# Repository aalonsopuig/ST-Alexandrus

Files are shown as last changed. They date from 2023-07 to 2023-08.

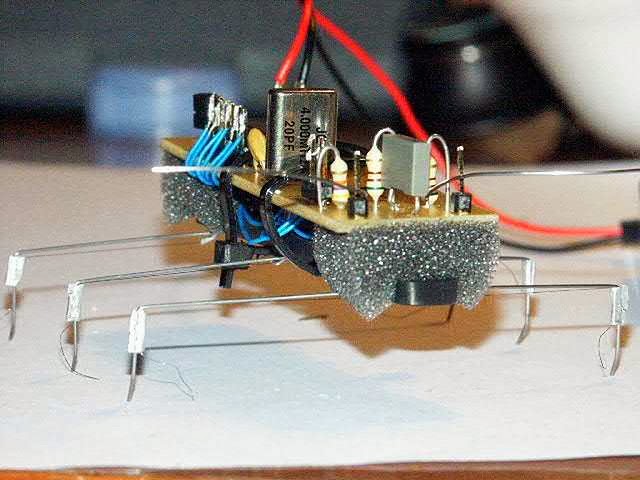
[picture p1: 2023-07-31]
st-alex.jpg

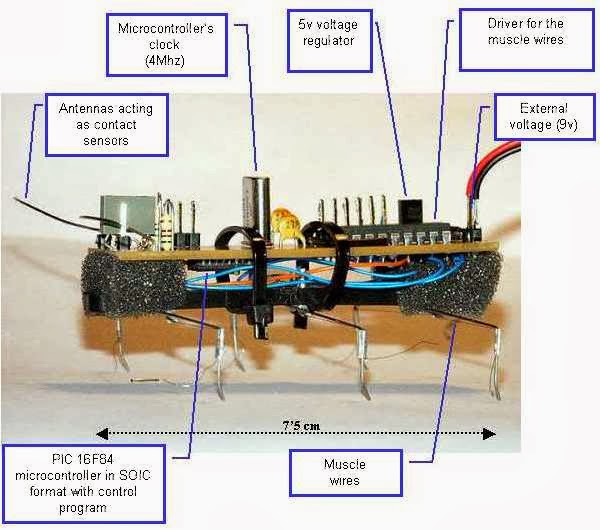
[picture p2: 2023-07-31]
enstparts.jpg

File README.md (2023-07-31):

ST-Alexandrus is an hexapod of one degrees of freedom by leg based on the structure of Stiquito (<a href="http://www.stiquito.com/">www.stiquito.com</a>). I made it on Dec. 2002<br />
<br />
The locomotion system is based on muscle wires of Nitinol.<br />
<br />
Its mission consists of moving as far as possible avoiding the obstacles that are in their way.<br />
<br />
<table align="center" cellpadding="0" cellspacing="0" class="tr-caption-container" style="margin-left: auto; margin-right: auto; text-align: center;"><tbody>
<tr><td style="text-align: center;"></td></tr>
<tr><td class="tr-caption" style="text-align: center;">ST-Alexandrus Robot</td></tr>
</tbody></table>
<br />
<b>Muscle Wires</b><br />
<br />
The muscle wire is an alloy (Nitinol) that belongs to the group of the so called materials with form memory. The wire is compressed between 3 and 5% of its length when warming up itself by the passage of an electrical current and return to its normal state when cooling off (annulling the passage of electrical current). The contraction is fast (0.5 sg), but the relaxation is slower as thicker is the muscle wire, varying between 0.7 sg for a wire of 37 micrometers and 14.5 sg for one of 375 micrometers.<br />
<br />
<div class="separator" style="clear: both; text-align: center;">
<object width="320" height="266" class="BLOGGER-youtube-video" classid="clsid:D27CDB6E-AE6D-11cf-96B8-444553540000" codebase="http://download.macromedia.com/pub/shockwave/cabs/flash/swflash.cab#version=6,0,40,0" data-thumbnail-src="https://ytimg.googleusercontent.com/vi/N188-MJZrzo/0.jpg"><param name="movie" value="https://youtube.googleapis.com/v/N188-MJZrzo&source=uds" /><param name="bgcolor" value="#FFFFFF" /><param name="allowFullScreen" value="true" /><embed width="320" height="266"  src="https://youtube.googleapis.com/v/N188-MJZrzo&source=uds" type="application/x-shockwave-flash" allowfullscreen="true"></embed></object></div>
<br />
These long times of relaxation and small ratios of compression will imply that the robot moves slowly, with very short and slowed down steps.<br />
<br />
<br />
<b>Legs structure</b><br />
<br />
The legs are made with steel wire and therefore they are relatively elastic.<br />
<br />
Each leg has an only muscle wire that moves backwards the leg when being compressed (applying electrical current).<br />
<br />
<div class="separator" style="clear: both; text-align: center;">
</div>
<br />
The meeting point between the leg and the ground is slightly inclined backwards to assure the adhesion to the ground in the backwards movements of the leg and to reduce this adhesion in the forwards movements of the leg, necessary to allow him to walk since when having an only degree of freedom, only could drag the legs over the ground.<br />
<br />
When we stop applying electrical current to the muscle wire it cools off and stretches to its rest position. Since the leg is of steel wire, its elasticity tends to move forwards the leg until its rest position.<br />
<br />
Due to this structure of legs the robot cannot walk backwards.<br />
<br />
<br />
<b>Electronic circuit</b><br />
<br />
Basically it is a control system by microcontroller PIC16F84 and a driver of 8 channels (open collector) of which will be used 6 to give to the muscle wires the current that need to be compressed.<br />
<br />
He has contact sensors (bumpers) in the frontal part (antennas) that allow to detect obstacles.<br />
<br />
Next is the electrical scheme:<br />
<br />
<div class="separator" style="clear: both; text-align: center;">
</div>
<br />
The circuit includes a diode to prevent errors with polarity when connecting the battery and a 5v regulator to be able to use external feeding to 9v.<br />
<br />
<div class="separator" style="clear: both; text-align: center;">
</div>
<br />
Terminals "PROG" allow ICSP programming (In Circuit Serial Programming) of the microcontroller already mounted in plate.<br />
<br />
Terminals "IZDA" (Left) and "DCHA" (Right) correspond to the connections to the muscle wires of the legs. All the muscle wires have on common end and the other connected to each one of these pins. The common end, that correspond with the union of the muscle wire with the leg of steel wire, will be connected to the positive of the battery, between the diode and the voltage regulator.<br />
<br />
<div class="separator" style="clear: both; text-align: center;">
</div>
<br />
&nbsp;<b>Software</b><br />
<br />
The programming has been made in C language, using the freeware cross compiler PICC Lite of HTSOFT<br />
<br />
The algorithm is simple. Simply it makes the robot move by moving the legs three by three so that they always form a support triangle. When one of the antennas detects an obstacle, the robot moves only the legs of a side one to one to force the turn since as it has been mentioned before, the robot cannot walk backwards.<br />
<br />
The code is suitably commented for its understanding.<br />
<br />
<br />

<br />

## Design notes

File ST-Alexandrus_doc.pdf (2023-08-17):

## ST-Alexandrus

ST-Alexandrus es un hexápodo de un grado de libertad por pata construido sobre la estructura de un Stiquito (www.stiquito.com).

El sistema de locomoción está basado en alambres musculares (muscle wires) de Nitinol. Las patas están formadas por alambres de acero.

Cada pata es controlada de forma independiente desde
una placa de control con microcontrolador PIC16F84.

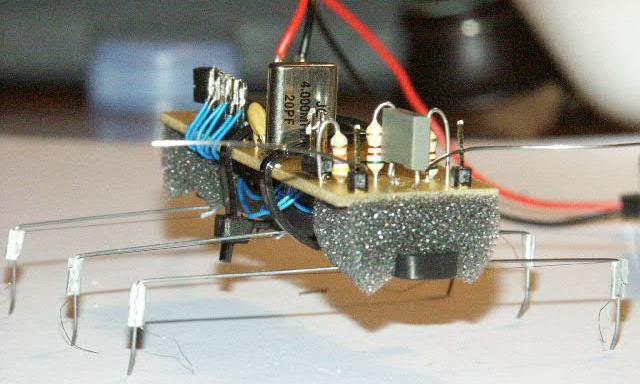
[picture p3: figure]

Posee sensores de contacto en la parte frontal que le permiten detectar obstáculos y aplicar algoritmos de giro.

### Construcción

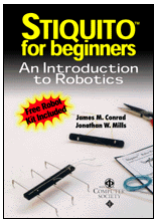
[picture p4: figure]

En primer lugar hay que montar la estructura de Stiquito. Dicha estructura se incluye como parte del libro “Stiquito for beginners” de James Conrad y Jonathan Mills.

Una vez montada la estructura se realiza el diseño de la electrónica. Básicamente se trata de un sistema de control por microcontrolador PIC16F84 y un driver de 8 canales para generar dar a los alambres musculares la corriente que necesitan para comprimirse.

A continuación se muestra es esquema eléctrico:

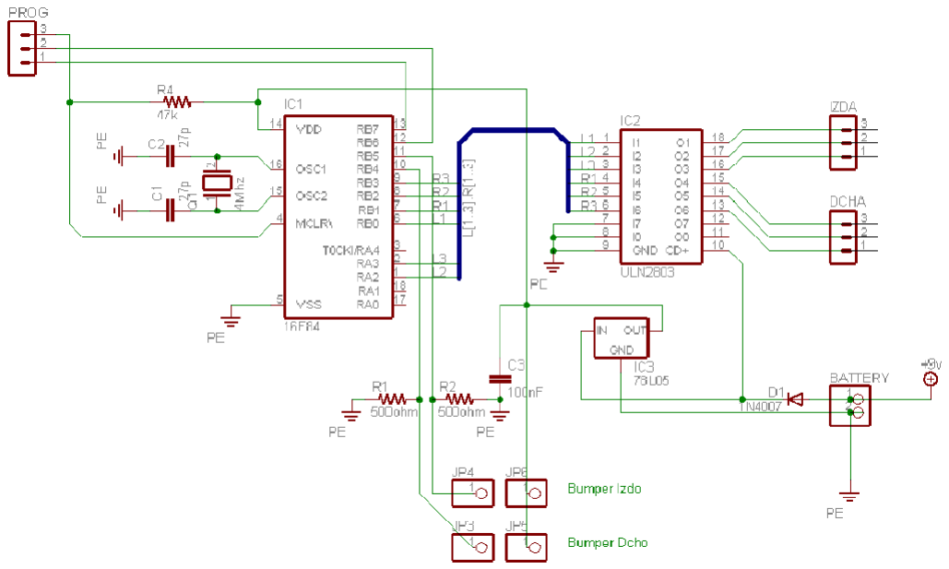
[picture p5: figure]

El circuito incluye un diodo para prevenir errores de polaridad al conectar la pila y un regulador a 5v para poder utilizar alimentación externa a 9v.

Los terminales “PROG” permiten la programación del microcontrolador desde una placa de grabación.

Los terminales “IZDA” y “DCHA” corresponden a las
conexiones a los alambres musculares de las patas. Todos
los alambres musculares tienen un extremo común y el otro conectado a cada una de estas patillas. El extremo común, que coincide con la unión con la pata de alambre de acero, quedará conectada al positivo de la batería, entre el diodo y el regulador de tensión.

Se montó el circuito en una protoboard y se programó el microcontrolador para comprobar el correcto resultado.

El diseño de la placa resultante es como sigue. En la
primera imagen se muestran las pistas y componentes. El
microcontrolador es el único componente que se situará en

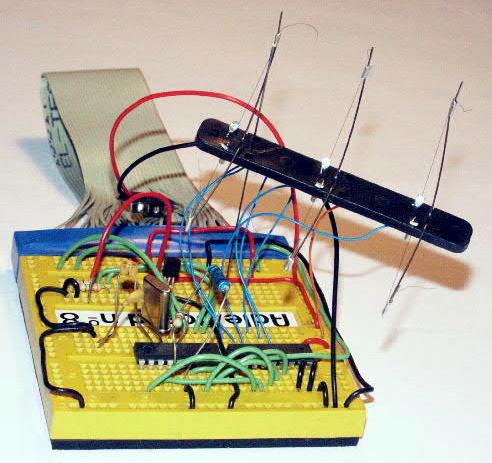
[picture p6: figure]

la parte inferior de la placa por ser de formato SOIC. Como se puede ver en la imagen hay un par de conexiones que deben hacerse mediante puentes.

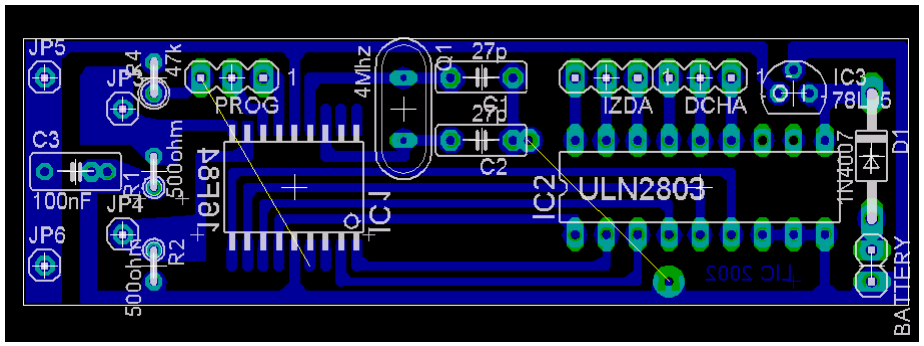
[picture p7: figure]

La segunda imagen corresponde a las pistas en inverso, tal como luego se imprimieron en transferible PNP.

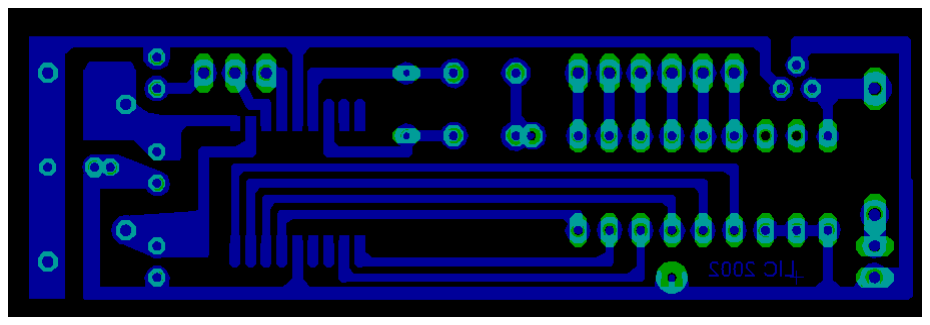
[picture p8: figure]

Una vez impreso en transferible PNP quedaría como se muestra a continuación:

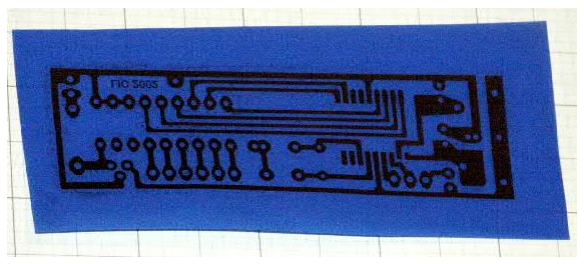
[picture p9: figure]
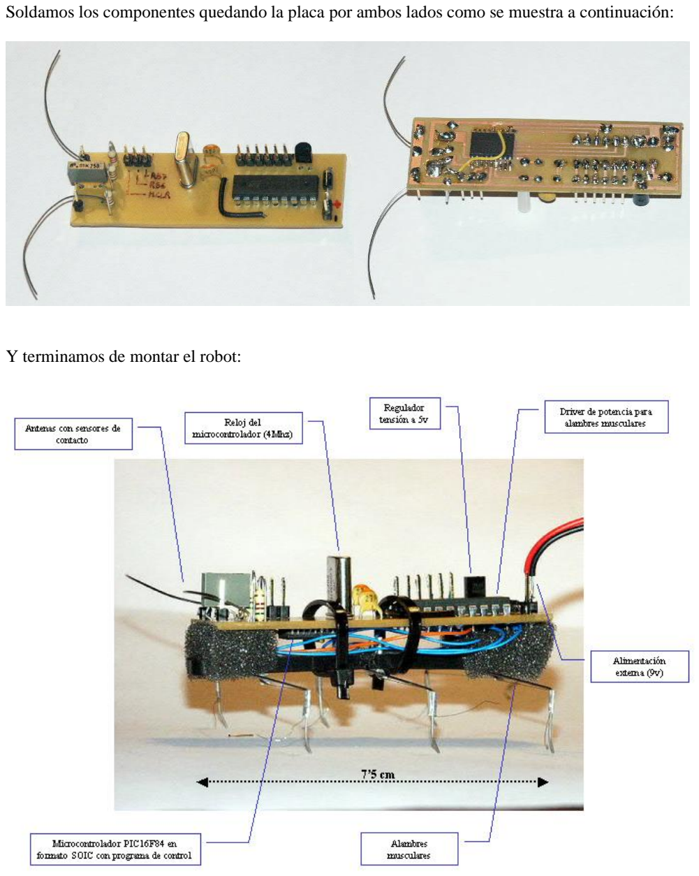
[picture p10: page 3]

Soldamos los componentes quedando la placa por ambos lados como se muestra a continuación:

Y terminamos de montar el robot:

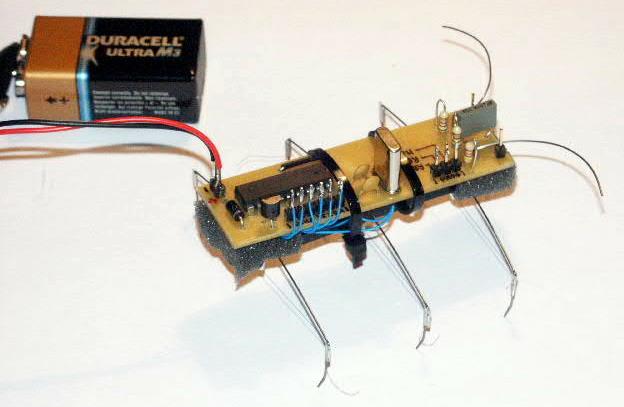
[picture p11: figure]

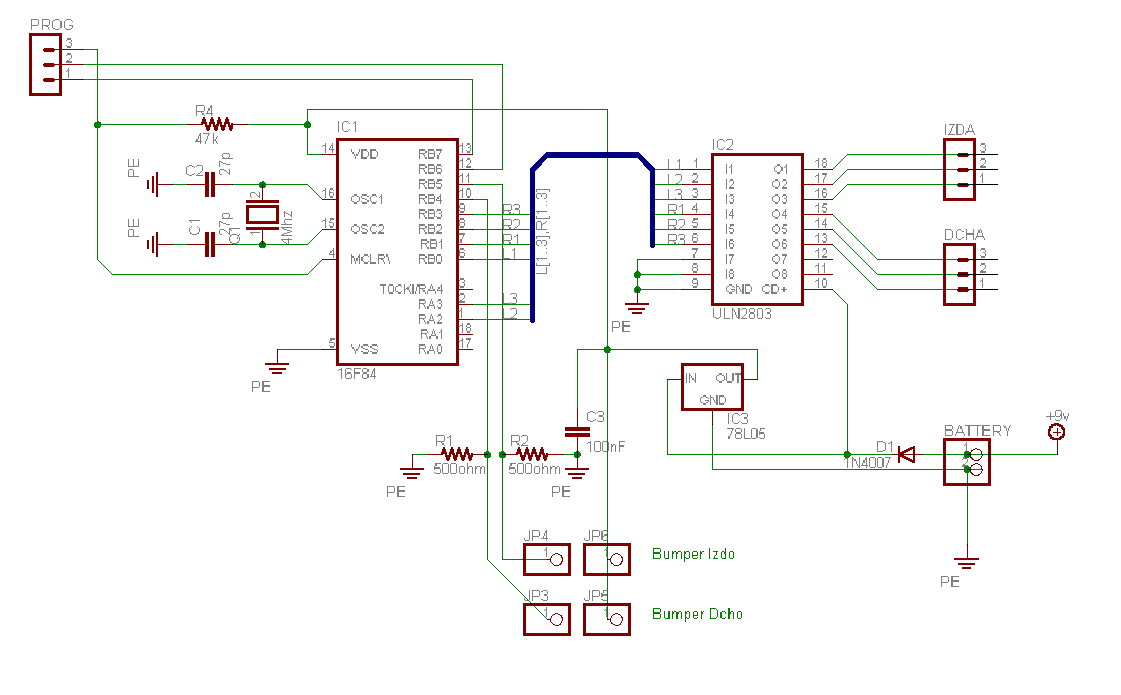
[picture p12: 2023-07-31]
scheme.png

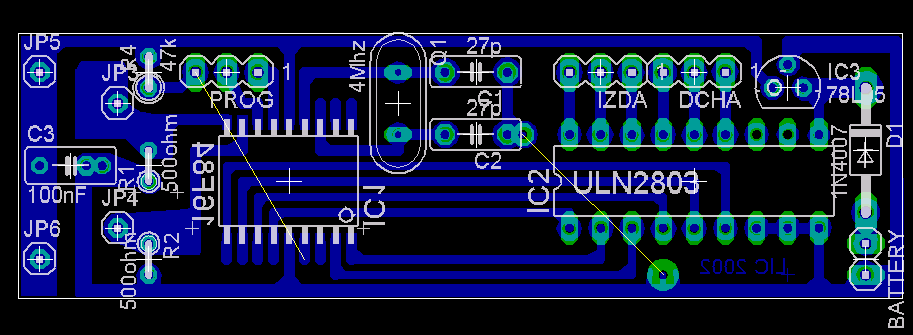
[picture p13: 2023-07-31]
board.png

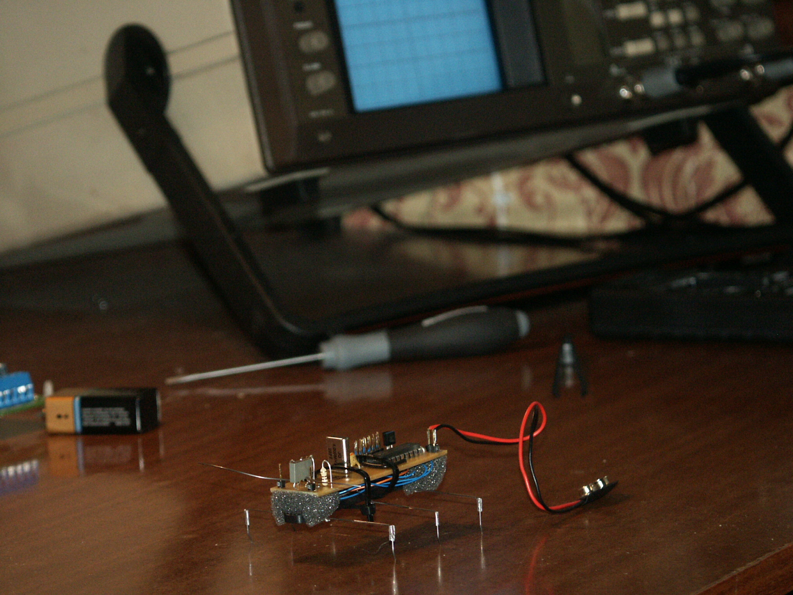
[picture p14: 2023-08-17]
Fotos/PICT0013.JPG

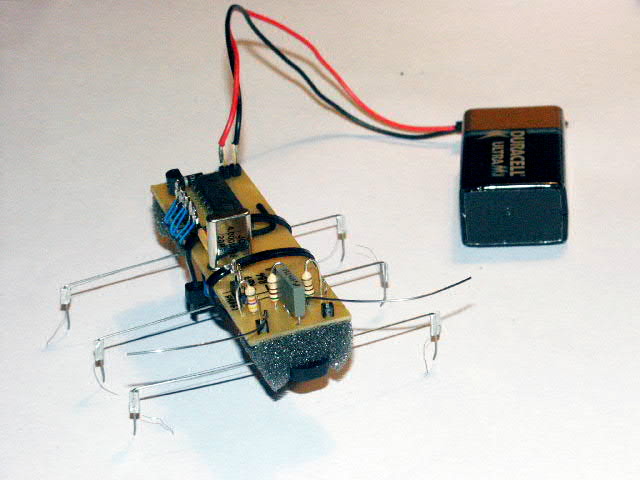
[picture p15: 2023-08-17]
Fotos/PICT0007b.JPG

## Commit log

2023-07-31 ST-Alexandrus Robot
    ST-Alexandrus is an hexapod of one degrees of freedom by leg based on the structure of Stiquito (www.stiquito.com). I made it on Dec. 2002
    The locomotion system is based on muscle wires of Nitinol.
    Its mission consists of moving avoiding the obstacles that are in their way.
    [Stiquito.brd, Stiquito.sch]
2023-08-17 adding more
    [Stiquito.brd, Stiquito.sch]
